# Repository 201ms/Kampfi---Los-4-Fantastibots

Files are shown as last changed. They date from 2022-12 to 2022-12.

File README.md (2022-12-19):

# Kampfi - 2022
Inspirado por los errores tecnicos y la mala suerte, Kampfi fue creado para maximizar la cantidad de cosas que podrian salir mal al hacer girar un pedazo de acero a la velocidad del ventilador en el radiador de un sedan. El equivalente battlebotiano de lo que sucede cuando le das un ak-47 a un mono.

Kampfi

## Integrantes
- Antonia Gutierrez - FCFM
- Benjamín Gonzalez - FCFM
- Joaquin Camhi - FCFM
- Matías Carvajal - FCFM

## Descripción del proyecto
Kampfi es un battlebot blindado con aluminio compuesto y acero. Como arma tiene instalada una hélice de acero en la parte delantera, la cual gira mediante un motor de 12 volts a una velocidad suficiente para romper el robot contrincante. Tiene un tren de traccion compuesto por 2 ruedas delanteras energetizadas por motores de 12 volts, y una rueda trasera no actuada. 

### Forma del robot
La forma triangular de Kampfi asegura que sea difícil de ser destruído por algun ataque superior (como ejemplo, un bot que ataca mediante un martillo), además le da la capacidad de ser facil de armar y desarmar en caso de que sean necesaria reparaciones, dado a que se compone unicamente de panales cuadrados y triangulares, y la base se encuentra conectada a la coraza mediante tornillos fáciles de remover.

### Estrategia utilizada
#### Ofensiva
Kampfi esta equipado de una hélice delantera angulada en 45° con respecto al horizonte. Para atacar se acerca a su victima y al activar el giro de la hélice es capas de destruír cualquier pieza impresa en filamento plastico, separar uniones entre paneles que componen la armadura, doblar corazas metalicas y penetrar pedazos de aluminio compuesto debido al perfil con puntas en las esquinas del arma. Para atacar se debe activar el arma para que empieze a girar y se debe conducir hacia el contrincante en un angulo, idealmente golpeando por el lado izquierdo para aprovechar que la helice gira en sentido antihorario e intentar levantar y desestabilizar al contrintante. 

#### Defensiva
Debido al lento movimiento del robot no es práctico intentar evitar ataques enemigos, la principal defensa es la ofensa: Resistir a los golpes enemigos mediante la coraza de aluminio compuesto y acero, e intentar aterrizar un golpe certero al mecanismo de transmision del arma del contrincante, idealmente desarmandolo. De forma experimental se ha determinado que la armadura es capaz de resistir ataques de armas tipo "spinner", cilindros o discos con perfiles girando a altas velocidades.

#### Uso del arma
La arma se puede activar o desactivar remotamente, se recomienda activar el arma previo al ataque para que gire a una velocidad suficiente como para hacer daño, y desactivar el arma una vez alcanzada una rotación suficiente para evitar gastar la batería principal del robot, dejando que la inercia rotacional del rectangulo de acero le proporcione el daño al enemigo. Si se activa el arma y debido a alguna resistencia (la helice esta atrapada en el cuerpo del contrincante, o en la malla del ring) no gira la helice se debe desactivar inmediatamente el arma, para evitar sobrecalentar los electronicos del robot, junto con el gasto de bateria asociado, el motor usado tiene una gran velocidad de rotacion pero bajo torque: Si no empieza a girar la hélice una vez activada el arma, lo mas probable es que nunca empieze a girar debido a que la resistencia es mayor al torque del motor.

#### Distribución de armadura
Las defensas del robot estan distribuidas de forma relativamente equitativa: El frente esta protegido por el motor de la helice y la helice en sí, los lados tienen aluminio compuesto, y debido a que hay una distancia de un par de centimetros de las laminas de este material y los componentes internos es difícil que se vean dañados por ataques laterales, la parte superior del robot es especialmente resistente a ataques de martillos como se explicó en la seccion "Forma del robot", y la parte trasera es protegida por dos barras paralelas de acero. Debido al peso del robot y a la forma de este, los ataques con objetivo de voltear al enemigo son ineficaces en Kampfi.

### Movimiento
El movimiento y la operación del robot se logran mediante una simple aplicación movil. 6 botones, 4 organizados en una cruz y 2 paralelos, abajo de esta, permiten el movimiento y uso del arma, respectivamente. Los botones de movimiento realizan la accion deseada mientras se presiona el botón (si se desea ir hacia adelante, se presiona el boton correspondiente y se suelta una vez llegado al punto deseado), y el arma opera mediante un toggle on/off: Un boton activa la rotación y otro la detiene. Se tomó la desición de no hacer que el mismo botón prenda y apague el arma por razónes de seguridad, para asegurar que siempre se puede apagar el arma con un boton, y así estar seguro que efectivamente se apagó el arma (ya que esta suele seguir girando una vez apagada debido a la inercia rotacional explicada previamente).

## Diagrama funcional
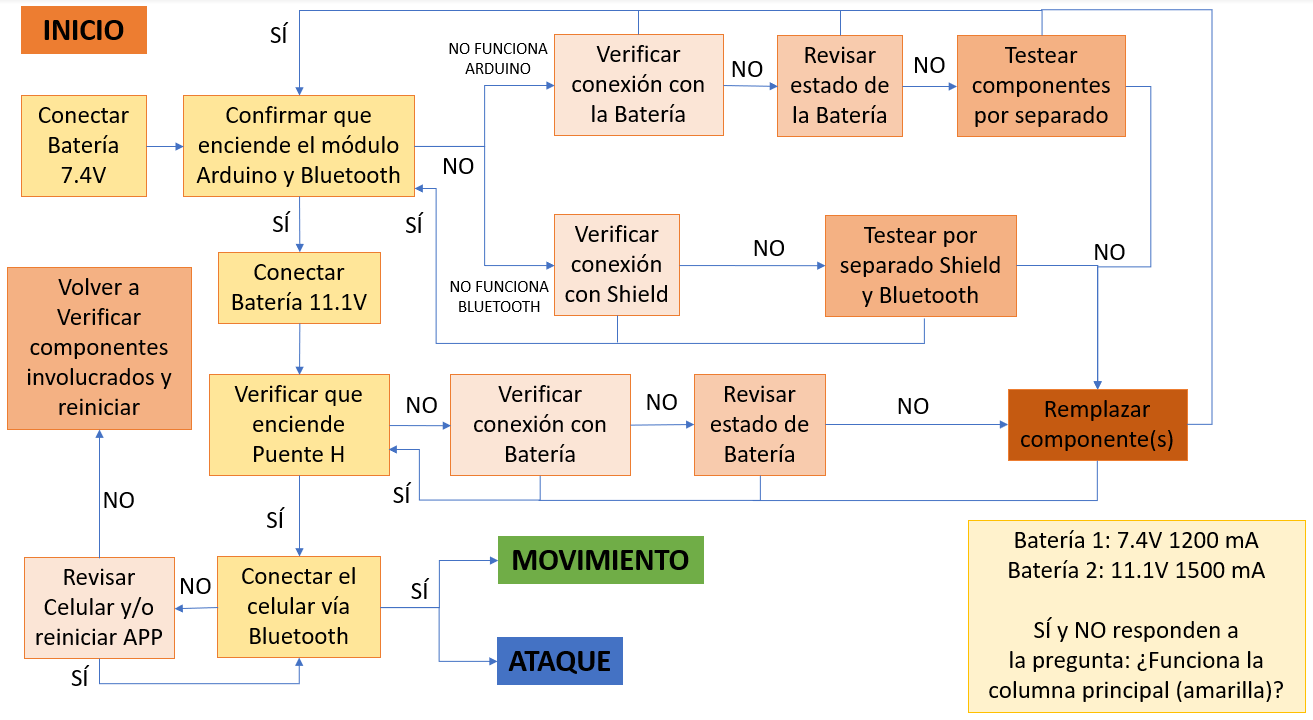
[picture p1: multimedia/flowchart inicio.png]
Diag. Inicio Bot


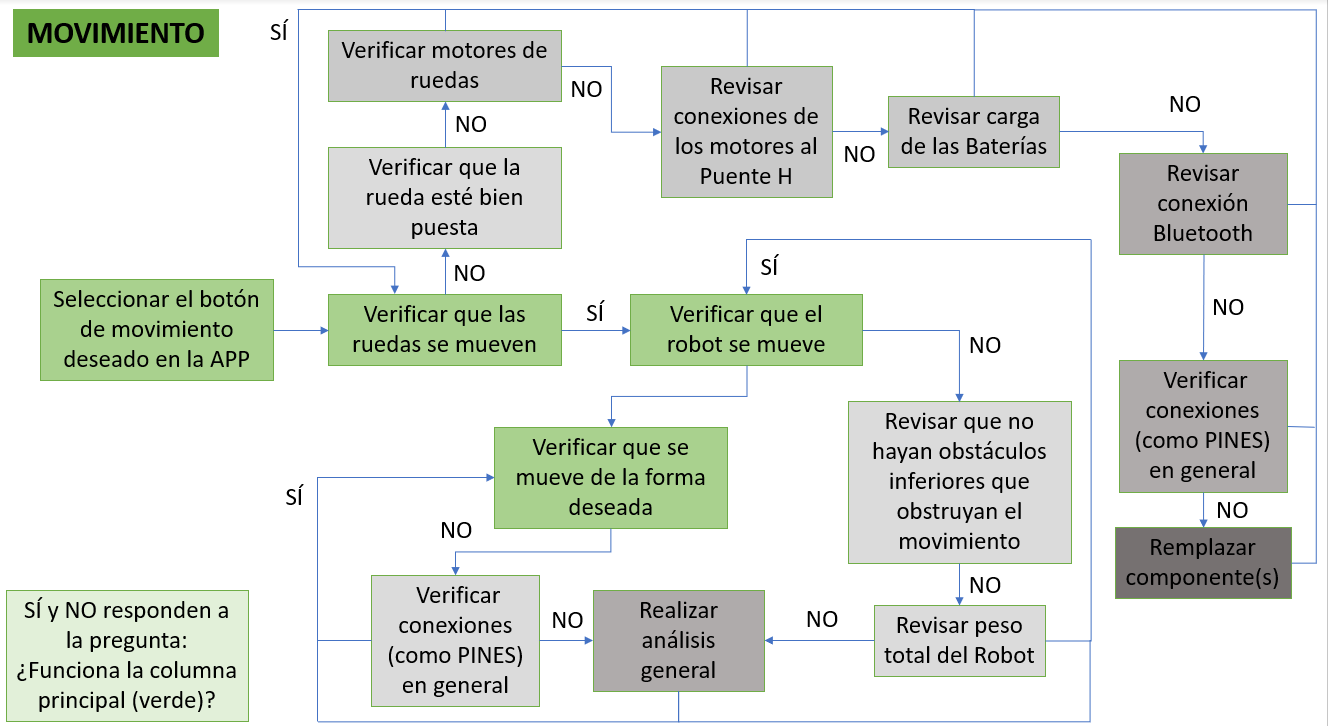
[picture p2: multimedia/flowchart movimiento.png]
Diag. Movimiento Bot


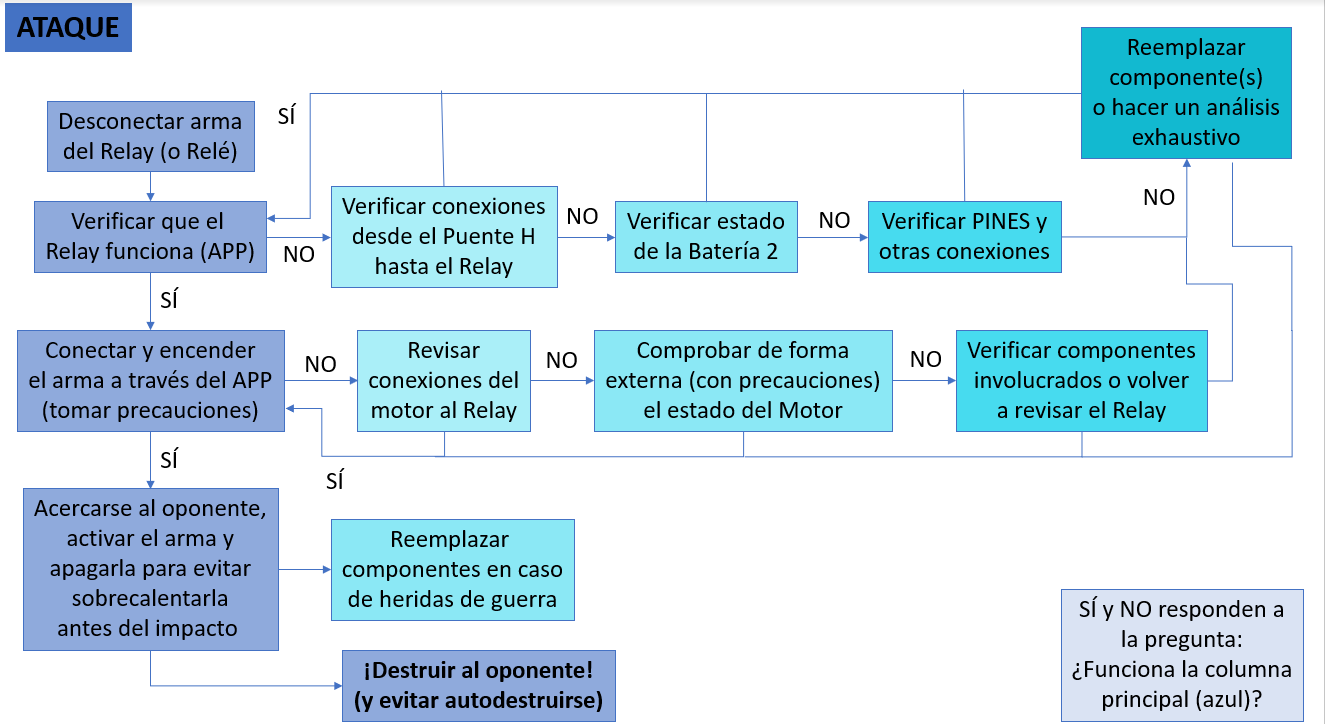
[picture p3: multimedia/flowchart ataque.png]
Diag. Ataque Bot


## Paso a Paso
### Materiales

- Plancha de aluminio compuesto
- Plancha de acero inoxidable cortada en rectangulos x3
- Puente H de 12V
- Relay 5Vdc de 1 canal
- Arduino Uno
- Regulador de voltaje 7 V a 5 V
- Motor de radiador (12V), u análogo.
- Filamento plastico PLA
- Bateria 11.1 V 1500mAide (o idealmente de alto mA por hora) 
- Bateria 7.4 V 1200 mA
- Cables
- Tornillos
- Tuercas
- Madera
- Pintura en Aerosol plateada y roja
- 2 motores de rueda 12 V + cajas de transferencia 
- 2 ruedas de goma

### Herramientas

- Taladro
- Router CNC
- Impresora 3D
- Llave inglesa
- Destornillador phillips
- Sierra Circular para madera
- Martillo
- Cautin, y estaño

### Procedimiento

1) Descargar todos los archivos ".f3z" de las piezas, el codigo ".ino" de arduino y el ".apk" de la app
2) Realizar el circuito del bot de acuerdo a los diagrama
3) Cortar las piezas de la base y la coraza en el Router CNC a través del archivo "piezas coraza.f3z" y "base.f3z"
4) Cortar piezas de madera (en archivo "ensamblado.f3z") que permiten las uniones del ensamble. Utilice su herramienta de mayor comodidad
5) Ensamblar los componentes en la base y armar la coraza. Para esto, guiarse por el archivo "ensamblado.f3z"
6) Asegurar todo en sus lugares, utilizar la máxima cantidad de tornillos sin llegar a dañar la madera
7) Comprobar que el circuito electrico funcione correctamente, guiarse a través de los diagramas
8) Ensamblar el arma a la coraza y unir esta parte con la base
10) Comprobar el funcionamiento de Kampfi con el diagrama funcional

Su Kampfi esta listo para funcionar.

**no nos hacemos responsables de fallas con las ruedas o daños ocasionados por el poco cuidado con el arma**

## Licencia
<br />Esta obra está bajo una <a rel="license" href="http://creativecommons.org/licenses/by-nc/4.0/">Licencia Creative Commons Atribución-NoComercial 4.0 Internacional</a>.

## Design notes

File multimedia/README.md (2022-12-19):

# Archivos multimedia de los battlebots

Batalla Free4All: https://youtube.com/shorts/aVzDHyngc24?feature=share

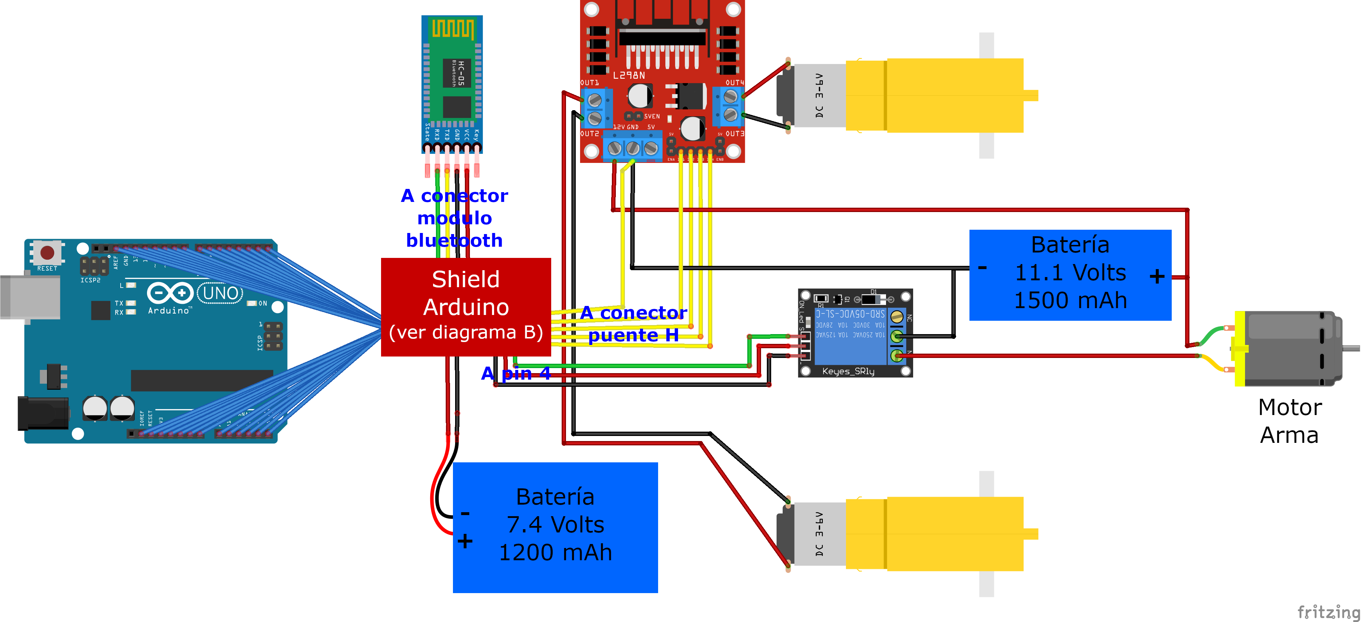
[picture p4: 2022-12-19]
diagrama/Diagrama Electromecánico A.png

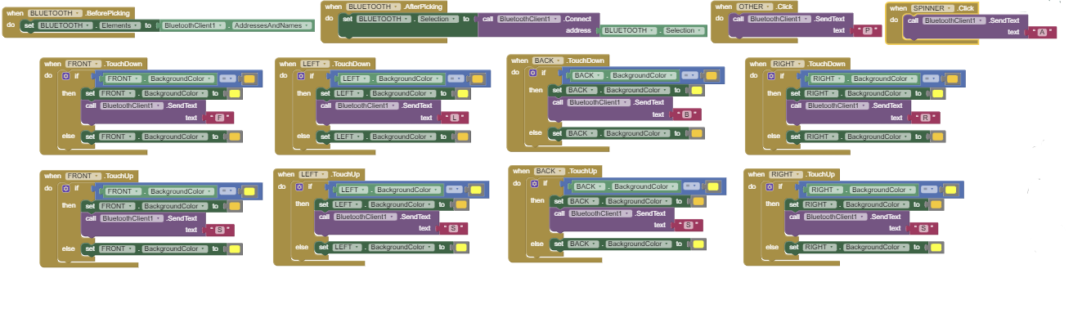
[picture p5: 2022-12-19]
codigos/APK/Kampfi_Blocks_APP.png

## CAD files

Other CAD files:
planos/Placa base.f3d

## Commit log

2022-12-19 Agregado flowcharts (cortesia de Mati)
2022-12-19 Corregido valores de mAh baterrias en diagrama A
